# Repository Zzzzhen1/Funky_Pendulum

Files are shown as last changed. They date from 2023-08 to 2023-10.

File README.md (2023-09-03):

# Funky_Pendulum
Inherited from Will and Jeppe. (Their github link)
Based on the project accomplished by Owen and Zhen during 2023 summer. Code developed by @Zzzzhen1. 
Any questions about the code please feel free to contact zy336@cam.ac.uk or leave in
dicussion session in this GitHub repository.
 
## General Description of the project. Should include the following features:

1. Schematics of the physical setup. (Possibly pictures and diagrams)
2. Complete safety measures.
3. What should students do to run the program. (Undecided yet: possibly use vscode or other editor space)
4. Possible changes that can be made in the program and how can students revert their changes. (In both python and Arduino)

## Experiment Setup

TODO: attach the pictures in the images folders here

## Upward Balancing Video

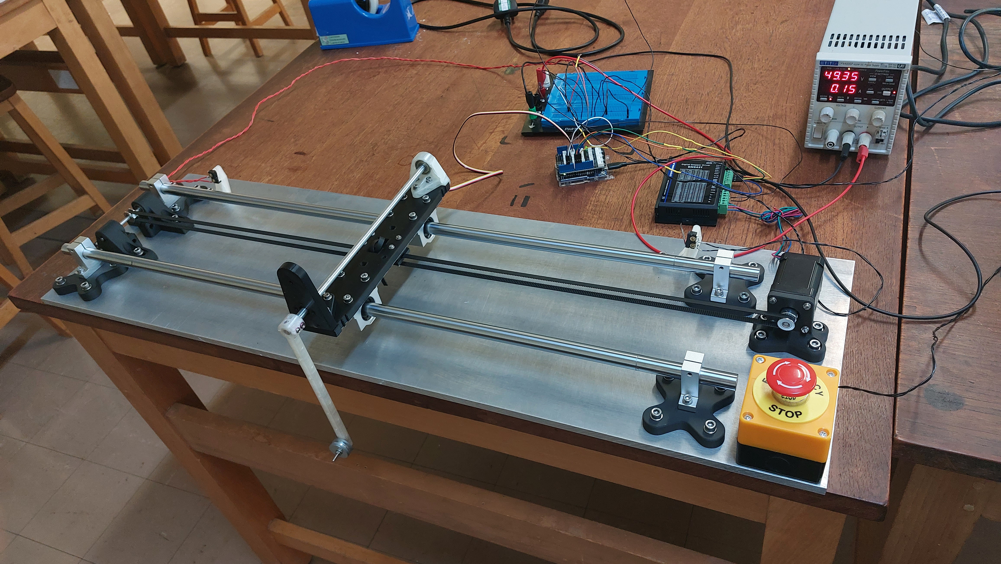
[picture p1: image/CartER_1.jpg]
Upward Balancing Video (https://youtu.be/zVNbTGS4LvY  "Upward Balancing Video")


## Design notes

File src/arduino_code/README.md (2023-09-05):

# Use Arduino IDE to upload the following file

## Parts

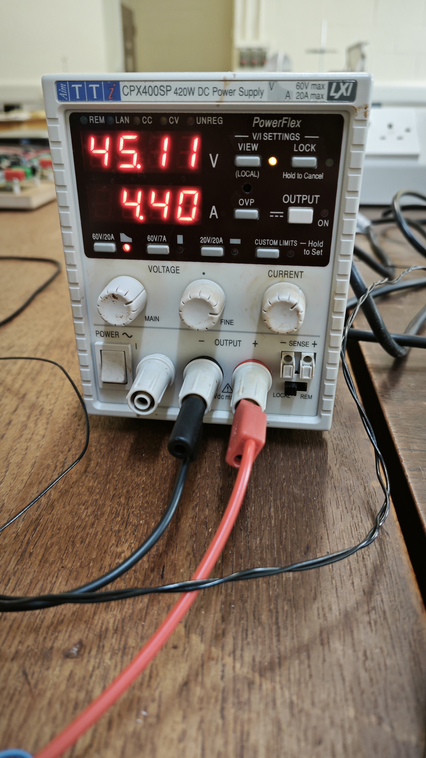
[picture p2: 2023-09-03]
image/Power_Supply_2_Need_Extra_Purchase.jpg

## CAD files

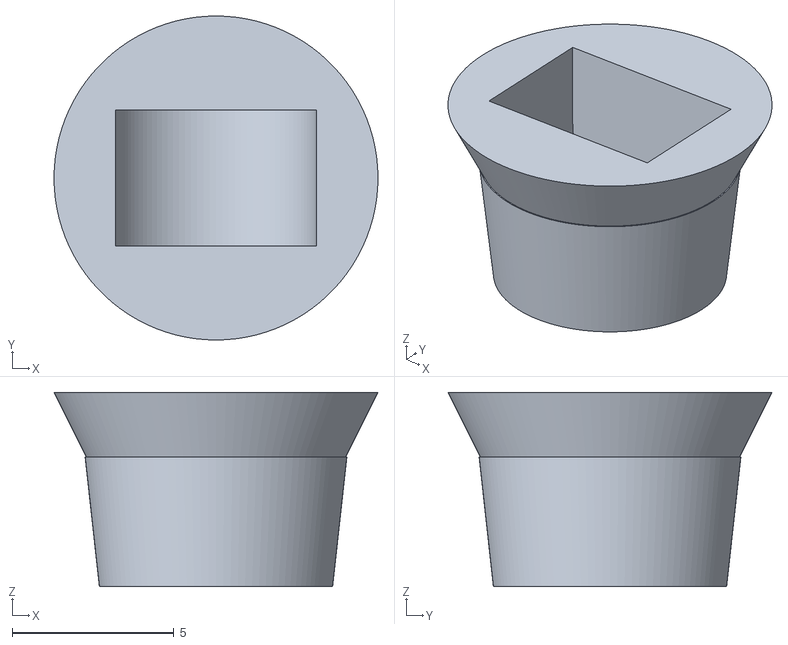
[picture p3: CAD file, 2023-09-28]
3D_Printing/stl/Magnet_Holder.stl
10.0 x 10.0 x 6.00

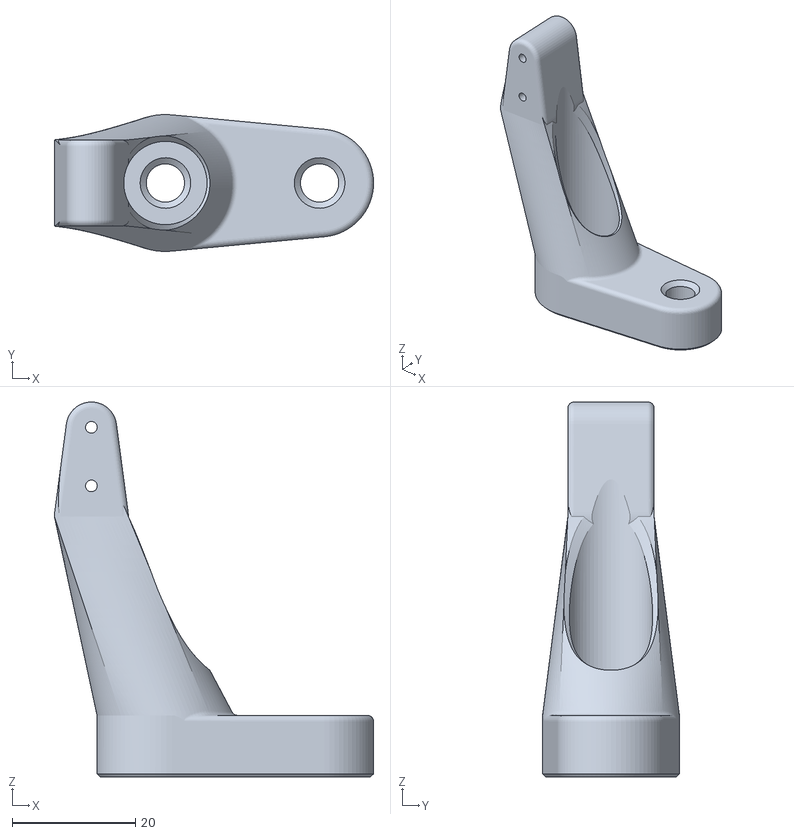
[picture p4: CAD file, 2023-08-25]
3D_Printing/stl/LimitSwitchFixture.stl
51.8 x 22.2 x 60.8

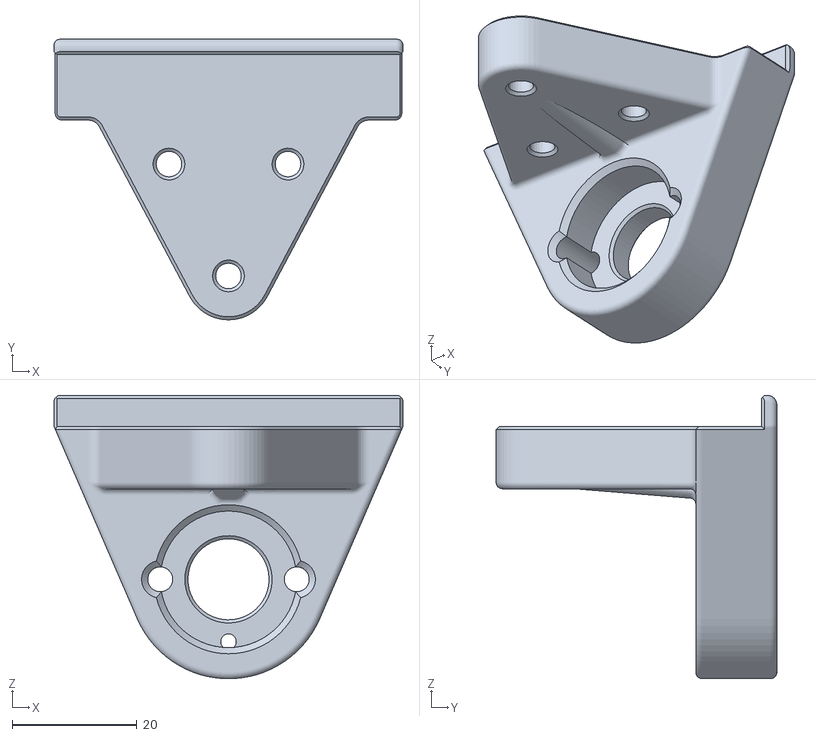
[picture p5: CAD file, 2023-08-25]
3D_Printing/stl/Rod_Holder_Back.stl
56.0 x 45.0 x 45.5

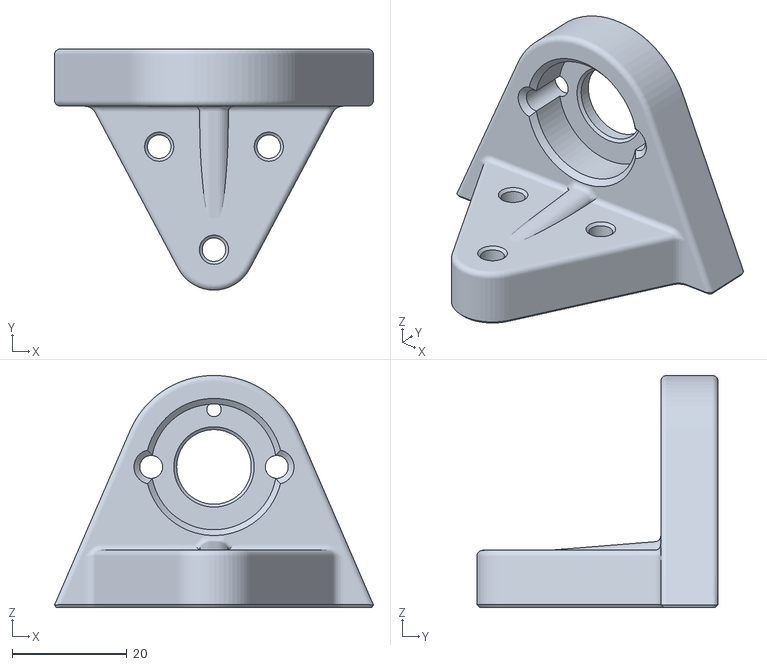
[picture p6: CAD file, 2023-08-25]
3D_Printing/stl/Rod_Holder_Front.stl
55.6 x 42.0 x 40.5

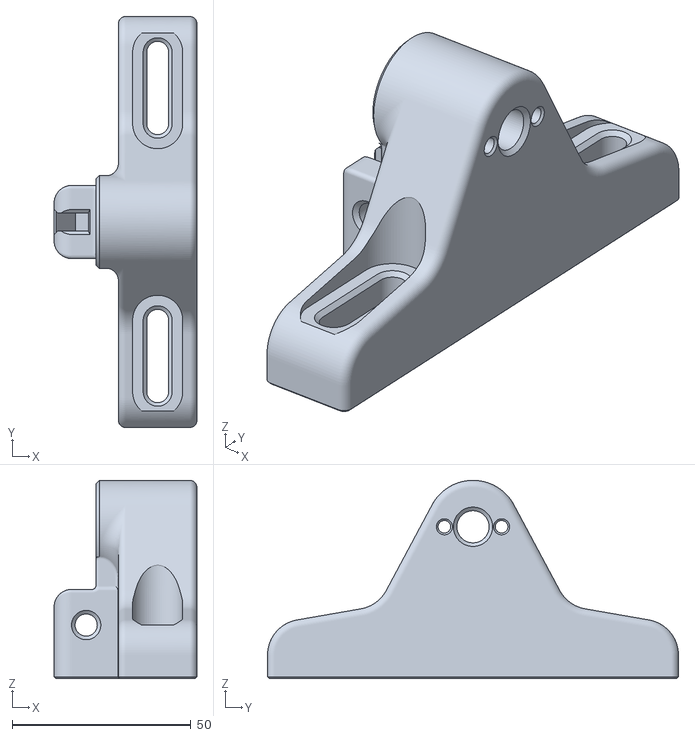
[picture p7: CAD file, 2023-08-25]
3D_Printing/stl/Pendulum_Idler.stl
40.0 x 115.0 x 55.5

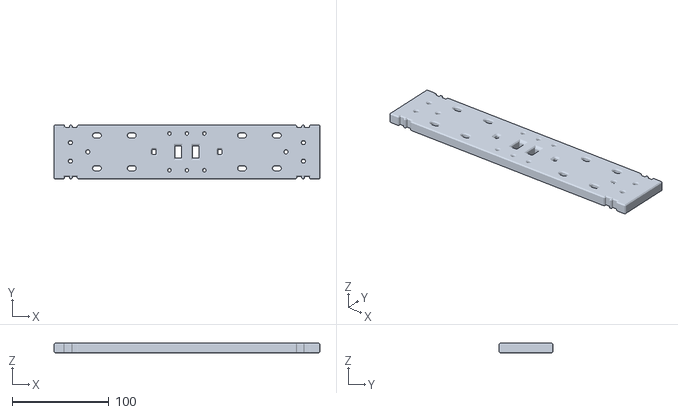
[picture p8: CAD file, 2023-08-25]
3D_Printing/stl/Base.stl
275.0 x 56.0 x 10.0

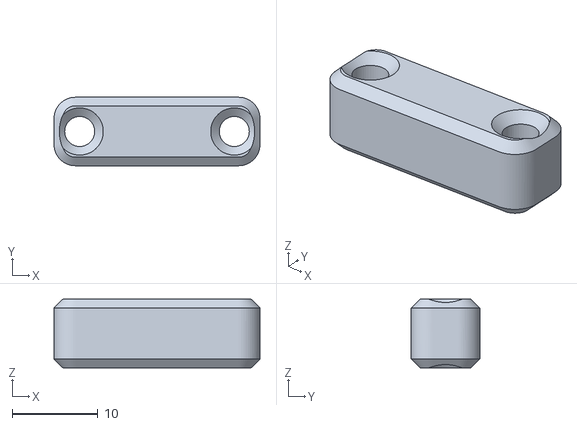
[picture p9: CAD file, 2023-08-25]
3D_Printing/stl/Belt_Fixture_Spacer.stl
24.0 x 8.00 x 8.00

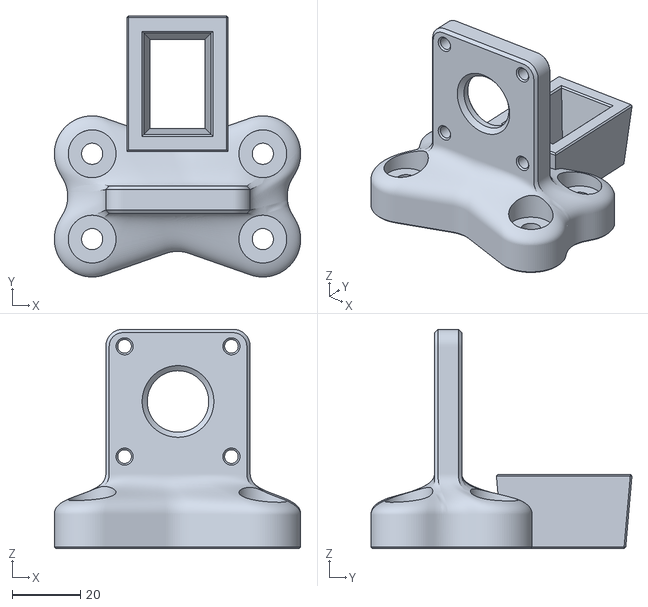
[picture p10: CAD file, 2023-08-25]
3D_Printing/stl/Stepper_Fixture.stl
72.2 x 76.5 x 64.3

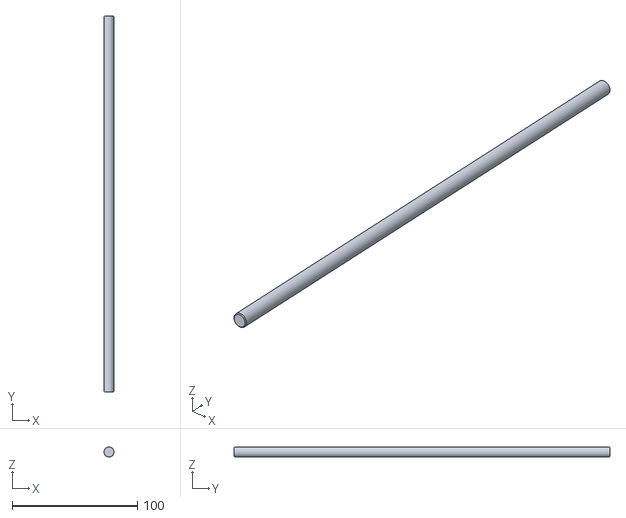
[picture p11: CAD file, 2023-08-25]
3D_Printing/stl/Pendulum_Rod.stl
8.00 x 300.0 x 8.00

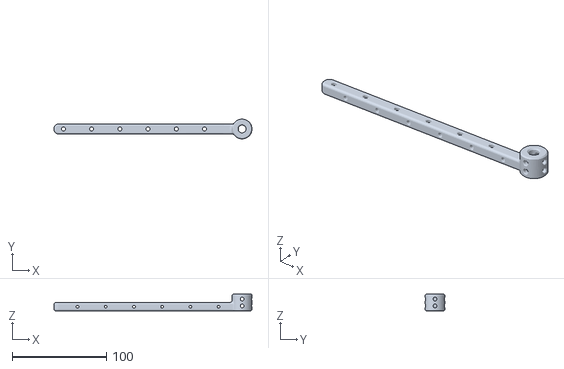
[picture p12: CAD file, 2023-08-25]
3D_Printing/stl/Pendulum_Arm.stl
210.5 x 21.0 x 18.0

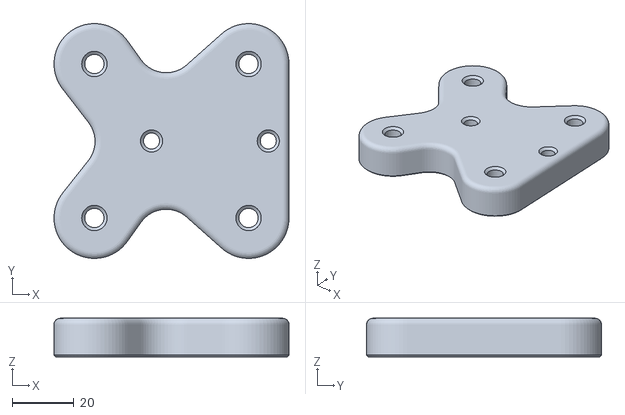
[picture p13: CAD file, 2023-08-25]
3D_Printing/stl/Rod_Clamp_Fixture.stl
76.3 x 76.2 x 12.5

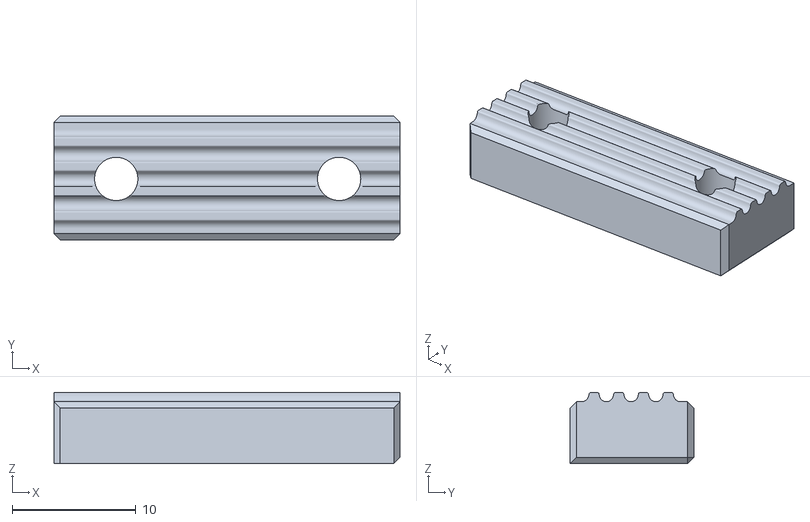
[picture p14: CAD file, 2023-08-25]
3D_Printing/stl/Belt_Fixture.stl
28.0 x 10.0 x 5.75

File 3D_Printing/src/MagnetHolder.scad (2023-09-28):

//defining some constant
magnet_radius = 3.1;
magnet_height = 4.2;
rod_radius = 4;
base_height_1 = 4;
base_height_2 = 2;
fac = 0.5; //45 deg inclination: easy for printing

module magnet(){
    cylinder(h = magnet_height, r = magnet_radius, center = true, $fn = 100);
}

module base(){
    union(){
        translate([0, 0, 0.5 * (base_height_1 + base_height_2)])
        cylinder(h = base_height_2, r1 = rod_radius, r2 = rod_radius + fac * base_height_2, center = true, $fn = 100);
        cylinder(h = base_height_1, r1 = 0.9 * rod_radius, r2 = 1.01 * rod_radius, center = true, $fn = 100);
    }
}

module holder_vertical(magnet_displacement){
difference(){
    base();
    #hull(){
        translate([0, 0, magnet_radius + magnet_displacement])
        rotate([90, 0, 0])
        magnet();
        translate([0, 0, magnet_displacement])
        rotate([90, 0, 0])
        magnet();
    }
}   
}
module holder_horizontal(magnet_displacement){
difference(){
    base();
    #hull(){
        translate([0, 0, magnet_radius + magnet_displacement])
        magnet();
        translate([0, 0, magnet_displacement])
        magnet();
    }
}   
}


holder_vertical(1.3);
//translate([15, 0, 0])
//holder_vertical(1.7);
//translate([0, 15, 0])
//holder_horizontal(1.3);
//translate([15, 15, 0])
//holder_horizontal(1.7);

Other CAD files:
3D_Printing/src/Base.f3d
3D_Printing/src/Belt_Fixture.f3d
3D_Printing/src/Belt_Fixture_Spacer.f3d
3D_Printing/src/Limit_Switch_Fixture.f3d
3D_Printing/src/Pendulum_Arm.f3d
3D_Printing/src/Pendulum_Idler.f3d
3D_Printing/src/Pendulum_Rod.f3d
3D_Printing/src/Rod_Clamp_Fixture.f3d
3D_Printing/src/Rod_Holder_Back.f3d
3D_Printing/src/Rod_Holder_Front.f3d
3D_Printing/src/Stepper_Fixture.f3d

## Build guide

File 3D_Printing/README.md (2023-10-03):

# Precaution to use these files in 3D printing
- The models used in the project are developed using Fusion 360, whose education license is free to access as a Cambridge student (still valid by 08/2023)
- For any changes user want to make in the system, please use the Fusion 360 software to access the files in the /3D_Printing/src/ folder.
- In the demo videos and images, the models are mostly 3D printed using Generic Tough PLA.
- For direct printing of the models, please use the files in /3D_Printing/stl/, which can be processed by any 3D slicer software (e.g., UltiMaker Cura), then generate the sliced version of the stl files for printing.
- The melting temperature of the Tough PLA is about **150C to 180C** (might be slightly different for different manufacturer), which can be melted by the running stepper motor. This might cause the loose band and lowered tension in the band.

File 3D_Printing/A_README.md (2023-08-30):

# Precaution to use these files in 3D printing
- The models used in the project are developed using Fusion 360, whose education license is free to access as a Cambridge student (by 30/08/2023)
- For any changes user want to make in the system, please use the Fusion 360 software to access the files in the /3D_Printing/src/ folder. (Currently missing the source code for the Pendulum_Idler, whose stl version exists in the /3D_Printing/stl/ folder)
- In the demo videos and images, the models are mostly 3D printed using Generic Tough PLA.
- For direct printing of the models, please use the files in /3D_Printing/stl/, which can be processed by any 3D slicer software (e.g., UltiMaker Cura), then generate the sliced version of the stl files for printing.
- The melting temperature of the Tough PLA is about 150C to 180C (might be slightly different for different manufacturer), which can be melted by the running stepper motor. This might cause the loose band and lowered tension in the band. It is better to attach a heat isolation pad between the PLA and the stepper motor.

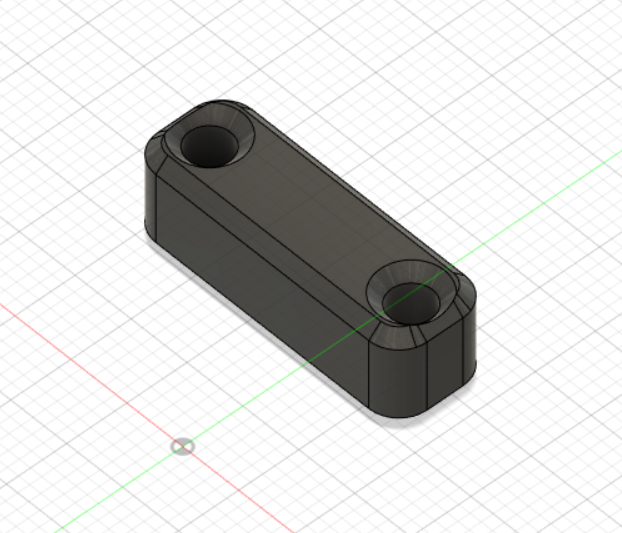
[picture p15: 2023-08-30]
3D_Printing/Image/Belt_Fixture_Spacer.PNG

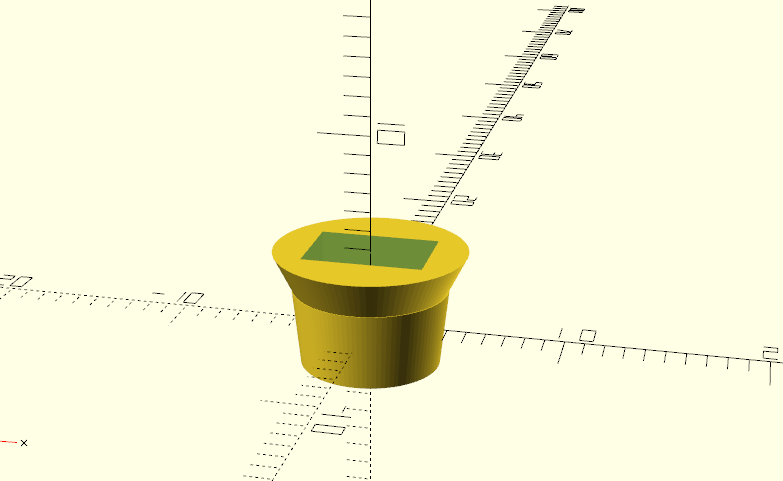
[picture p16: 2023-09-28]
3D_Printing/Image/Magnet_Holder.PNG

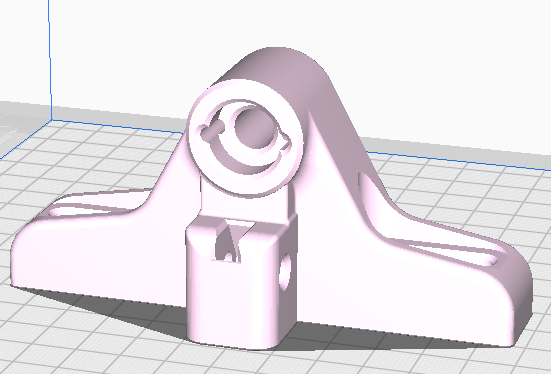
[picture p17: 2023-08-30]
3D_Printing/Image/Pendulum_Idler.PNG

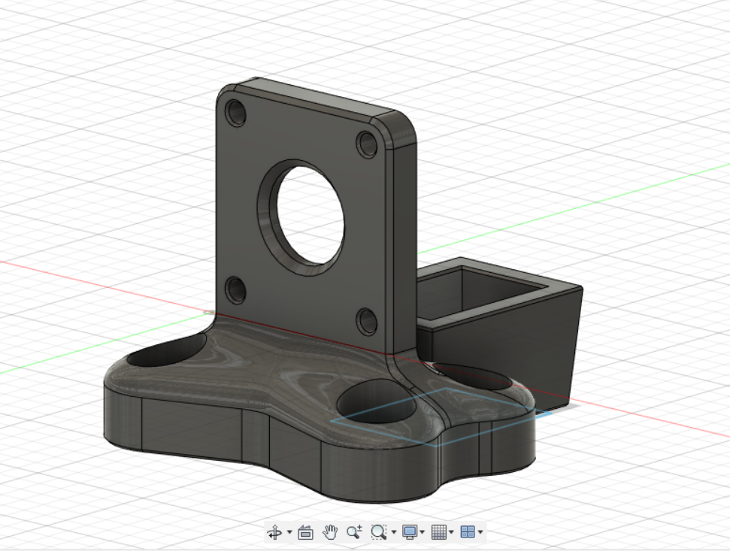
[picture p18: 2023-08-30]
3D_Printing/Image/Stepper_Fixture.PNG

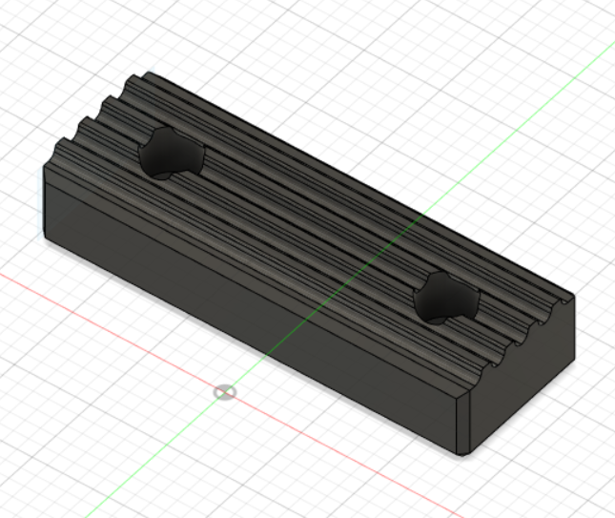
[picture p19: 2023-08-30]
3D_Printing/Image/Belt_Fixture.PNG

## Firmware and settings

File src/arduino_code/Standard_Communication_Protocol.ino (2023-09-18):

// General description:


// Include all the necessary head files
#include "Arduino.h"
#include "AS5600.h"
#include "Wire.h"
#include "math.h"
#include "AccelStepper.h"
#include "ezButton.h"

// Initialization of Arduino Board
const int baudrate = 230400;

// General intialization parameters
#define MAX_SIZE 20  // Maximum size of the input array

// This motor model (NEMA 17) is a typical bipolar 1.8deg (200steps/rev) motor.
// Therefore the corresponding microstep is 200 / STEPS, which needs to be taken into account
// Also, there's a maximum amount of steps each loop can take to avoid jittering! Will be tested later
#define STEPS 400 // Number of steps per revolution [Currently microsteps have not been implemented, so the position would be integer steps]
const int step_fac = int(STEPS / 200);  // Think of the configuration as 200 steps per revolution, but with 200/STEPS as minimum division.
const int max_steps = 200;              // Maximum number of steps per loop, which also determines the precision of cart position per loop.

// Define the stepper using accelstep
#define step_pin 8      // Connect to the PUL pin on the driver
#define step_vcc_pin 9  // Connect to constant 5V output PIN
#define dir_pin 10      // Connect to the DIR pin on the driver
#define dir_vcc_pin 11  // Connect to constant 5V output PIN
AccelStepper stepper(AccelStepper::DRIVER, step_pin, dir_pin);

// Stepper related variables
int distance = 0;                // Total Rail distance
int pos_L = 0;                   // Position of the left switch
int pos_R = 0;                   // Position of the right switch
float pos_cart = 0;              // Current position of the cart. Changing in every cycle
float pos_cart_prev = 0;         // Previous position of the cart. Used to update the new move function
float pos_cart_target = 0;       // Target position of the cart. Won't change until the target has been reached.
float pos_integ = 0;             // Integral control bit for position
float vel = 0;                   // Cart velocity calculated using buffer arrays.
const float speed_lim = 4000.0;  // Maximum speed, also the speed for the run() method
float run_speed = 800.0;        // Speed that the stepper normally runs at
const float accel = 120000.;    // Pre-set acceleration
long int safe_steps = 50;        // Safe distance to both switches
const float safe_speed = 500.0;  // Avoid crushing into the swtich too hard
float steps = 0.;                // Target position or relative movement, depends on the situation
float temp_speed = 4000.;        // Temporal speed limit
float temp_accel = 120000.;     // Temporal acceleration

// NR stage variable
double omega = 0.;             // Driven frequency of the cart
const int freq_size = 10;      // Maximum number of frequencies this cart can run at
double omega_list[freq_size];  // Multiple driven frequencies of the cart
float amp = 0.;                // Initial sinosuidal amplitude (steps) used for NR amplitude scan
float amp_0 = 50.;             // Initial sinosuidal amplitude (steps) used for constant oscillation
const float amp_swing = 100.;  // Constant swing up amplitude (steps) [Currently disabled]
float phase = 0.;              // Initial angle phase (in terms of the cart position)

// Buffer related variables and arrays
int buf_ind = 0;                                 // Buffer index of the loop. Keeps increasing over the time
int current_ind = 0;                             // Current index of the buffer array. current_ind = buf_ind % buf_len
int temp_ind = 0;                                // Temporary index variable
const int buf_len = 100;                         // Length of the buffer arrays
const int circ_buf_len = 2 * buf_len;            // Length of the circular buffer arrays
const int pos_vel_len = 2;                       // Number of points to calculate velocity (see get_velocity())
double circ_buffer_time[circ_buf_len] = { 0 };   // Circular buffer of the time to recover the sample history.
double circ_buffer_angle[circ_buf_len] = { 0 };  // Circular buffer of the angle to recover angular history
int circ_buffer_position[circ_buf_len] = { 0 };  // Circular buffer of the cart position to recover the position history.

// PID parameters [Needs another fine tuning because the setup for the motor has changed]
float Kp = 1000;       //Reasonable: 300-2000
float Ki = 0;          //Reasonable: 300-1700
float Kd = 4;          //Reasonable: 2-10
float Kp_pos = -0.05;  //Reasonable: 0.001-0.1
float Ki_pos = 0.04;   //Reasonable: 0.001-0.1
float Kd_pos = -0.01;  //Reasonable: 0.0001-0.005

// Define the button
#define Lbtn_pin 5        // Left switch pin
#define Rbtn_pin 4        // Right switch pin
ezButton Lbtn(Lbtn_pin);  // Left switch initiation
ezButton Rbtn(Rbtn_pin);  // Right switch initiation

//Equilibrium measuring and time-related variables
double current_time = 0.;            // Current time in seconds
double previous_time = 0.;           // Previous time in seconds
const long sample_div = 50;          // Sampling division. Default: 50 ms --> sampling rate ~= 20 Hz
unsigned long sample_time = 0;       // Sampling time variable to enable sampling rate.
unsigned long sample_time_prev = 0;  // Sampling time variable to enable sampling rate.

// Button state change detect
bool state_Lbtn = 1;       // Instant state of the left button
bool state_Rbtn = 1;       // Instant state of the right button
bool state_Lbtn_prev = 1;  // State of the left button of the previous loop
bool state_Rbtn_prev = 1;  // State of the right button of the previous loop
bool state_L = 1;          // Proper state variable that detects the change of state of the left button
bool state_R = 1;          // Proper state variable that detects the change of state of the right button

// Initialization of communication
String message = "";  // Used for receiving general messages
String junk = "";     // Junk message string
String cmd = "";      // Command string

// Useful counting variables
int center_count = 0;

// Flag indication of different stages
// During reset, these flags need to be set to original values
bool flag_command = 1;  // Receiving command from PC
int int_cmd;
bool flag_reset = 0;          // Reset command flag
bool flag_center = 0;         // Center command flag
bool flag_measure = 0;        // Angle Measure command flag
bool flag_setSpeed = 0;       // Test out the max speed and then set the speed_lim for the stepper motor -- command flag
bool flag_freq_scan = 0;      // Frequency Scan command flag
bool flag_pid = 0;            // PID Control command flag
bool flag_NR = 0;             // Normalised resonance command flag
bool flag_print_command = 1;  // Print the command once
bool flag_exit = 0;           // Exit current stage. Go back to function selection menu
bool flag_init_ang_cul = 1;   // Detect the initial cumulative angle --> used to the zero the angle measurement
// Center stage
bool flag_L = 1;  // Center stage flag for left switch
bool flag_R = 1;  // Center stage flag for right switch
// NR stage
bool flag_omega = 1;  // Receive a input command
bool flag_amp = 1;    // Receive a input command

// PID stage
bool flag_swing_request = 1;  // Default: ask for swing up and ask for parameter?
bool flag_swing = 0;          // Whether execute swing up strategy. Default: no swing up strategy
bool flag_pid_input = 1;      // Default: ask for new parameters
bool flag_eq_measure = 1;     // Measure the equilibrium angle
bool flag_switch_regime = 1;  // Switch to inversion control (with swing up strategy)
// SetSpeed stage
bool flag_setSpeed_request = 1;

// Initialize the angle sensor
void init_angle_sensor() {
  //any AS5600 specific initiations to be called here
}
AS5600 angle_sensor;
float ang = 0;            // Angle measurement
double ang_cul = 0;       // Cumulative angle measurement
double init_ang_cul = 0;  // Initial cumulative angle measurement
double ang_vel = 0;       // Angular velcity measurement
double ang_dev = 0;       // Angle deviation
double ang_eq = 0;        // Equilibrium angle
double ang_integ = 0;     // Integral control bit for angle

// Initialize the stepper
void init_stepper(float spd_lim, float accl) {
  pinMode(step_vcc_pin, OUTPUT);
  pinMode(dir_vcc_pin, OUTPUT);
  digitalWrite(step_vcc_pin, HIGH);
  digitalWrite(dir_vcc_pin, HIGH);
  stepper.setSpeed(safe_speed);
  stepper.setMaxSpeed(spd_lim);
  stepper.setAcceleration(accl);
  stepper.setCurrentPosition(0);
}

// Initialize the buttons
void init_button() {
  // Initialize the debounce time of the buttons
  Lbtn.setDebounceTime(10);
  Rbtn.setDebounceTime(10);
}

// Print the menu through the serial
void menu_print() {
  Serial.println("Cart pendulum functions: ");
  Serial.println("Enter 0 to reset the arduino board.");
  Serial.println("Enter 1 to begin the cart position centering.");
  Serial.println("Enter 2 to begin the natural frequency and quality factor measuring.");
  Serial.println("Enter 3 to set max running speed and max acceleration.");
  Serial.println("Enter 4 to begin the frequency scan.");
  Serial.println("Enter 5 to begin the PID control of inverted pendulum.");
  Serial.println("Enter 6 to begin the normalised resonance.");
}

// Begin execution of command print
void command_print(int num) {
  if (flag_print_command) {
    flag_print_command = 0;
    switch (num) {
      case 0:
        Serial.println("Resetting...");
        break;
      case 1:
        Serial.println("Begin centering.");
        break;
      case 2:
        Serial.println("Begin the natural frequency and quality factor measuring.");
        break;
      case 3:
        Serial.println("Begin the speed and acceleration setting.");
        break;
      case 4:
        Serial.println("Begin the frequency scan.");
        break;
      case 5:
        Serial.println("Begin the PID control.");
        break;
      case 6:
        Serial.println("Begin the normalised resonance.");
        break;
    }
    delay(500);
  }
}

// Reset the flags to original state
void reset(bool center = true) {
  flag_command = 1;
  flag_reset = 0;
  flag_center = 0;
  flag_measure = 0;
  flag_setSpeed = 0;
  flag_freq_scan = 0;
  flag_pid = 0;
  flag_NR = 0;
  flag_print_command = 1;
  flag_exit = 0;
  flag_init_ang_cul = 1;
  flag_L = 1;
  flag_R = 1;
  flag_omega = 1;
  flag_amp = 1;
  flag_swing_request = 1;
  flag_swing = 0;
  flag_pid_input = 1;
  flag_eq_measure = 1;
  flag_switch_regime = 1;
  flag_setSpeed_request = 1;
  if (center) {
    center_count = 0;
  }
  amp = 0.;
  amp_0 = 50.;
  buf_ind = 0;
  temp_ind = 0;
  memset(circ_buffer_angle, 0., sizeof(circ_buffer_angle));
  memset(circ_buffer_time, 0., sizeof(circ_buffer_time));
  memset(circ_buffer_position, 0., sizeof(circ_buffer_position));
  memset(omega_list, 0., sizeof(omega_list));
  ang_eq = 0.;
  init_ang_cul = 0.;
  sample_time = 0;
  sample_time_prev = 0;
  Serial.flush();
}

// Make sure there is only one command being executed each loop
void single_command_check() {
  int sum = flag_reset + flag_center + flag_pid + flag_measure + flag_NR + flag_setSpeed + flag_freq_scan;
  switch (sum) {
    case 0:
      Serial.println("No command detected.");
      delay(500);
      flag_command = 1;
      break;
    case 1:
      break;
    default:
      Serial.println("More than one command detected. Resetting the values.");
      delay(500);
      reset();
      break;
  }
}

// Reset the cart. This is a safety measure.
void cart_reset(bool kill = true) {
  stepper.stop();
  delay(500);
  stepper.setSpeed(safe_speed);
  stepper.runToNewPosition(0);
  // Final moment print to trigger stage changes in laptop
  if (kill) {
    Serial.println("Kill switch hit.");
  }
}

// Check whether a input string is fully made of numbers
bool isNumber(String str) {
  for (int i = 0; i < str.length(); i++) {
    if (!isDigit(str.charAt(i))) return false;
  }
  return true;
}

// Check whether a input string is a float number
bool isFloat(String str, bool neg = false) {
  int dot_count = 0;
  int neg_count = 0;
  for (int i = 0; i < str.length(); i++) {
    if (str.charAt(i) == '.') {
      dot_count += 1;
    } else if (str.charAt(i) == '-') {
      neg_count += 1;
    } else if (!isDigit(str.charAt(i))) {
      return false;
    }
    if (dot_count > 1) return false;
    if (neg_count > 1) return false;
    if (neg_count == 1 && !neg) return false;
  }
  return true;
}

// Used in the setSpeed stage, appoint the input two values 
bool isTwoFloat(String str){
  String temp_str = "";
  int comma_count = 0;
  for(int i = 0; i < str.length(); i++){
    if(comma_count > 1){
      temp_speed = speed_lim;
      temp_accel = accel;
      return false;
    }
    if(str.charAt(i) == ','){
      comma_count += 1;
      if(isFloat(temp_str)){
        temp_speed = temp_str.toFloat();
      }else{
        temp_speed = speed_lim;
        temp_accel = accel;
        return false;
      }
      temp_str = "";
    }else{
      temp_str += str.charAt(i);
    }
  } 
  if(isFloat(temp_str)){
    temp_accel = temp_str.toFloat();
  }else{
    temp_speed = speed_lim;
    temp_accel = accel;
    return false;
  }
  return true;
}
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
void loop() {
  if (flag_command) {
    if (Serial) {
      menu_print();
      cmd = read_cmd();
      if (flag_command == 0) {
        single_command_check();
        command_print(int_cmd);
      }
    } else {
      message = read_msg();
      if (message == "connection") {
        Serial.println("Successfully Connected");
        delay(500);
      }
    }
  } else {
    // Initiate the button in the loop
    Lbtn.loop();
    Rbtn.loop();
    // 1 for released and 0 for pressed
    state_Lbtn = Lbtn.getState();
    state_Rbtn = Rbtn.getState();
    state_L = state_change_L();
    state_R = state_change_R();

    if (flag_reset) {
      reset();
    } else if (flag_center) {
      center();
    } else if (flag_pid) {
      pid();
    } else if (flag_measure) {
      measure();
    } else if (flag_NR) {
      NR();
    } else if (flag_setSpeed) {
      setSpeed();
    } else if (flag_freq_scan){
      freq_scan();
    }
    state_Lbtn_prev = state_Lbtn;
    state_Rbtn_prev = state_Rbtn;
  }
}

// Some control functions
// Runs the cart centering
void center() {
  if (Serial) {
    if (state_L && state_R) {
      if (flag_L && flag_R) {
        stepper.setSpeed(safe_speed);
        stepper.move(-1);
        stepper.runSpeedToPosition();
      } else if (!flag_L && flag_R) {
        stepper.setSpeed(safe_speed);
        stepper.move(1);
        stepper.runSpeedToPosition();
      } else if (!flag_L && !flag_R) {
        // Calculate and move to the central position. Then, set this position as zero.
        distance = pos_R - pos_L;
        stepper.setSpeed(run_speed);
        stepper.runToNewPosition(pos_L + int(distance / 2));
        flag_center = 0;
        center_count += 1;
        flag_command = 1;
        Serial.print(center_count);
        Serial.print(",");
        Serial.print(distance);
        Serial.println("");
        stepper.setCurrentPosition(0);
        delay(1000);
        reset(false);
        init_stepper(speed_lim, accel);
      }
    } else if (!state_L) {
      pos_L = stepper.currentPosition();
      stepper.move(1);
      stepper.runSpeedToPosition();
      stepper.stop();
      stepper.setSpeed(safe_speed);
      stepper.runToNewPosition(pos_L + safe_steps);
      flag_L = 0;
    } else if (!state_R) {
      pos_R = stepper.currentPosition();
      stepper.move(-1);
      stepper.runSpeedToPosition();
      stepper.stop();
      stepper.setSpeed(safe_speed);
      stepper.runToNewPosition(pos_R - safe_steps);
      flag_R = 0;
    } else {
      stepper.setSpeed(run_speed);
    }
  } else {
    reset();
  }
}

// Runs of the PID control of the pendulum
void pid() {
  if (Serial) {
    if (flag_swing_request) {
      Serial.println("Do you want to turn up swing up strategy? type in (y/n)");
      message = read_msg();
      if (message == "y") {
        Serial.println("Continue with swing up strategy.");
        flag_swing = 1;
        flag_swing_request = 0;
        stepper.move(200);
        delay(500);
      } else if (message == "n") {
        Serial.println("Continue without swing up strategy.");
        flag_swing = 0;
        flag_swing_request = 0;
        delay(500);
      } else if (message == "Terminate") {
        Serial.println("Terminate the process.");
        cart_reset();
        reset();
      } else {
        delay(500);
        Serial.println("Invalid command, please try again.");
        delay(500);
      }
    } else {
      if (flag_pid_input) {
        pid_print();
        Serial.println("");
        Serial.println("Resume (ENTER r) or ENTER six numbers split by commas without spaces");
        Serial.println("For example: 1000,0,4,-0.05,0.04,-0.01");
        Serial.println("In this order:Kp_ang,Ki_ang,Kd_ang,Kp_pos,Ki_pos,Kd_pos");
        Serial.println("[Scroll up to see previous values]");
        Serial.println("Before press ENTER, make sure either the pendulum is stable at downright or upright position!");
        message = read_msg();
        if (pid_receive()) {
          pid_print();
          Serial.println("Start inversion control.");
          flag_pid_input = 0;
        } else if (message == "Terminate") {
          Serial.println("Terminate the process.");
          cart_reset();
          reset();
        } else {
          delay(500);
          Serial.println("Invalid input, please Try Again");
          delay(500);
        }
      } else {
        if (flag_eq_measure) {
          if (flag_swing) {
            ang_eq = get_cumulative_angle();
          } else {
            ang_eq = get_cumulative_angle();
          }
          ang_cul = get_cumulative_angle();
          ang_eq = rectify_angle();
          flag_eq_measure = 0.;
        } else {
          pid_control_run(flag_swing);
        }
      }
    }
  } else {
    cart_reset();
    reset();
  }
}

// PID stage stepper control, print through serial: time, angle and position (all with velocity)
void pid_control_run(bool flag) {
  if (state_L && state_R) {
    current_ind = buf_ind % buf_len;
    current_time = millis() / 1000.;
    sample_time = millis();
    ang_cul = get_cumulative_angle();
    ang_eq = rectify_angle();
    ang_dev = ang_cul - ang_eq;
    ang_vel = get_angular_velocity();

    cart_run_max();

    pos_cart = stepper.currentPosition();
    pos_cart_target = stepper.targetPosition();
    vel = get_velocity();

    cart_run_max();

    circ_buffer_position[current_ind] = pos_cart;
    circ_buffer_angle[current_ind] = ang_cul;
    circ_buffer_time[current_ind] = current_time;
    circ_buffer_position[current_ind + buf_len] = pos_cart;
    circ_buffer_angle[current_ind + buf_len] = ang_cul;
    circ_buffer_time[current_ind + buf_len] = current_time;

    if (sample_time - sample_time_prev >= sample_div) {
      sample_time_prev = sample_time;
      Serial.print(current_time, 5);
      Serial.print(",");
      Serial.print(ang_dev, 4);
      Serial.print(",");
      Serial.print(pos_cart, 1);
      Serial.print(",");
      Serial.print(ang_vel, 4);
      Serial.print(",");
      Serial.print(vel, 4);
      Serial.println("");
    }

    if (flag) {
      // with swing up strategy
      if (flag_switch_regime) {
        // Do the swing up
        steps = int(amp_swing * (ang_dev));
        stepper.move(steps);
        cart_run_max();
        if (abs(abs(ang_dev) - M_PI) < 0.05 * M_PI && abs(ang_vel) < 0.5) {
          ang_eq = ang_eq + M_PI;
          ang_eq = rectify_angle();
          flag_switch_regime = 0;
        } else if (abs(abs(ang_dev) - M_PI) < 0.05) {
          cart_reset(false);
          delay(5000);  // Wait for manual stablisation
        }
      } else {
        // Do the control
        if (Ki != 0.) {
          ang_integ = ang_integ_calc();
        }
        if (Ki_pos != 0.) {
          pos_integ = pos_integ_calc();
        }
        steps = int(Kp * ang_dev + Ki * ang_integ + Kd * ang_vel - Kp_pos * pos_cart - Ki_pos * pos_integ - Kd_pos * vel);
        stepper.move(steps);
        cart_run_max();
      }
    } else {
      // without swing up strategy
      // Do the control
      if (Ki != 0.) {
        ang_integ = ang_integ_calc();
      }
      if (Ki_pos != 0.) {
        pos_integ = pos_integ_calc();
      }
      steps = int(Kp * ang_dev + Ki * ang_integ + Kd * ang_vel - Kp_pos * pos_cart - Ki_pos * pos_integ - Kd_pos * vel);
      stepper.move(steps);
      cart_run_max();
    }
    pos_cart_target = stepper.targetPosition();
    if (pos_cart_target <= -int(distance / 2) + safe_steps || pos_cart_target >= int(distance / 2) - safe_steps) {
      cart_reset();
      reset();
    }
    buf_ind += 1;
    previous_time = current_time;  // Record the begin time of this loop. For test Only.
  } else {
    cart_reset();
    reset();
  }
}

// Runs the angle measurement
void measure() {
  if (Serial) {
    ang_cul = get_cumulative_angle();
    previous_time = current_time;
    current_time = micros() / 1000000.;
    sample_time = millis();
    if (sample_time - sample_time_prev >= sample_div) {
      sample_time_prev = sample_time;
      Serial.print(current_time, 6);
      Serial.print(",");
      Serial.println(ang_cul, 4);
    }
  } else {
    reset();
  }
}
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

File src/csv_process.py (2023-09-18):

'''This is in general the data analysis class, currently compatible with the 
   measure and scan for response data analysis'''
import numpy as np
import matplotlib.pyplot as plt
import matplotlib as mpl
import pandas as pd
import os, csv, tkinter
from statistics import mean, stdev
from scipy.fft import fft, fftfreq
from scipy.signal import find_peaks
from scipy.optimize import curve_fit
plt.rcParams['axes.grid'] = True
plt.rcParams["figure.autolayout"] = True
mpl.use('TkAgg')

def damp_sin(time, gamma, omega, phi, amp, offset):
    '''Fit to the natural frequency measurement plot'''
    return amp * np.exp(- 0.5 * gamma * time) * np.sin(2 * np.pi * omega * time + phi) + offset

def sinusoid(time, omega, phi, amp, offset):
    '''Fit to the amplitude response scan plot'''
    return amp * np.sin(2 * np.pi * omega * time + phi) + offset

class data_analysis():
    
    '''Analysis class to analyse the data
    
    -----------------
    Attributes
    -----------------
    1. default buffer length of 16 * 65536
    2. default directory given by os.getcwd()
    3. a set of flags to indicate the stage of the analysis
    process
    4. a dictionary of properties, keys are assigned by the
    a list of headers
    
    Methods
    -----------------
    1. clear_flag(): 
        reset all the flags to their original state
    2. clear_data(): 
        clear all the data
    3. load_csv():
        load all the csv files from the input directory, returns 
        True if there is any csv file, False otherwise. This method
        will also turn up the flags for the csv type based on the
        header of the csv file
    4. read_csv(file_name, flag_pid = False):
        Args: 
            file_name: the name of the csv file
            flag_pid: whether the csv file is a pid type file, if True,
            read_csv will read the values starting from a different row
        Yields: 
            read the csv file and store the data in the data array
            update the properties dictionary
        Returns: 
            True if the csv file is read successfully, False otherwise
            (including negative time stamp, and sometimes empty file)
    5. check_csv_type():
        check whether all the csv files are of the same type, returns
        True if all the csv files are of the same type, False otherwise
    6. load_data(row, file):
        Args:
            row: a row of data from the csv file
            file: the csv file name
        Yields:
            load the data into the data array, delete the files if negative
            time stamp is detected
    7. clean_data(file):
        Yields:
            rotate the circular buffer to the correct starting time stamp
            and return the data array
    8. restore_figure(start_index = 0, end_index = -1):
        Args:
            start_index: the starting index of the data to be plotted
            end_index: the ending index of the data to be plotted
        Yields:
            restore the figure for the scan type data
    9. fft_index_list(time, fft_length, sampling_div):
        Args:
            time: the time array
            fft_length: the length of the fft
            sampling_div: the sampling interval
        Returns:
            index_list: the list of indices for the fft
            avg_spacing: the average time spacing, which determines
            the maximum frequency (refer to the Nyquist-Shannon sampling)
    10. general_fft(time, angle, position, fft_length, sampling_div):
        Args:
            time: the time array
            angle: the angle array
            position: the position array
            fft_length: the number of points used for fast fourier transform
            sampling_div: the desired sampling interval
        Returns:
            fft_angle: the fourier transform of the angle array
            fft_position: the fourier transform of the position array
            fft_freq: the frequency array
            avg: the average time spacing
    11. phase_rectify(phase):
        Args:
            phase: the phase to be rectified
        Returns:
            a phase in the range of -0.5 * pi to 1.5 * pi
    12. phase_calc(fft_freq, omega, fft_angle, fft_pos, interpolation = True):
        Args:
            fft_freq: the frequency array
            omega: the driving frequency in Hz
            fft_angle: the fourier transform of the angle array
            fft_pos: the fourier transform of the position array
            interpolation: whether to use interpolation to calculate the phase
        Returns:
            phase: the phase in the range of -0.5 * pi to 1.5 * pi
    13. scan_fit(time, angle, amp_range):
        Args:
            time: the time array
            angle: the angle array
            amp_range: the range of the amplitude to be fitted
        Returns:
            popt: the optimized parameters to fit the sinusoidal function
            pcov: the covariance matrix
    14. scan_fft_plot(axs, start_index = 0, end_index = -1):
        plot the phase curve and fft on the axes objects
    15. scan_process(axes, start_time, end_time, rolling_time):
        calculate the phase and amplitude of the scan data
        based on the input time range and rolling time
    16. scan_plot(file, block = True):
        plot two graphs:
        1. The angle-time graph with best fit line and parameters
        2. The phase curve and cumulated error
        And save the timestamp, the amplitude of the best-fit, and the
        phase with errors to a csv file
    17. save_scan_data(exp_data, file):
        save the scan data to a csv file
    18. measure_plot(file, block = True):
        plot the angle-time graph with best fit line and parameters
        And save the timestamp, the optimized parameters to a csv file
    19. save_measure_data(exp_data, file):
        save the measure data to a csv file
    20. main():
        the main function of the data analysis class
        '''
    
    def __init__(self):
        self.buffer_length = 16 * 65536 # The buffer length of the data
        self.dirc = os.getcwd() # Get the csv file directory, either by input
        self.csv_list = [] # A list of csv file names
        self.data_flag_dict = {
            'measure': False,
            'scan': False,
            'pid': False,
            
        }
        self.properties = {} # A dictionary of numbers read from the header
        self.header = [
            'special_info',
            'start_time',
            'omega',
            'multiple_omega',
            'amplitude',
            'phase/pi',
            'multiple_phase/pi',
            'time,angle,position,angular_velocity,cart_velocity',
            'Kp',
            'Ki',
            'Kd',
            'Kp_pos',
            'Ki_pos',
            'Kd_pos',
        ]
        self.data = np.zeros((5,self.buffer_length), dtype = float)
        self.count = 0
        self.phase_list = []
        self.amp_list = []
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

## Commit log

2023-08-23 Upload the latest arduino code (version 6.1) and made some changs to the control Pendulum_Control_Console.py
2023-08-30 Add files via upload
    Fusion 360 source code
    [Base.f3d, Belt_Fixture.f3d, Belt_Fixture_Spacer.f3d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]
2023-09-01 Update the todo list and upload a test file for multiple_omega case
    [NR-10-59-45.csv]
2023-09-04 update the arduino_code
2023-09-04 Update the manual phase fix
    [Pendulum_Control_Console.py]
2023-09-05 update the kill method for the writer thread
2023-09-05 update the correct real_time_phase
    [Pendulum_Control_Console.py]
2023-09-07 update with the new command. decided to add jolt to PID
2023-09-08 cancel the thread_check in NR stage
2023-09-11 update the check function in the arduino code
2023-09-11 update the arduino code
2023-09-12 fix the bug of setSpeed
    [Standard_Communication_Protocol.ino]
2023-09-15 update with the arduino code
2023-09-18 correct the terminal output
    [Pendulum_Control_Console.py]
